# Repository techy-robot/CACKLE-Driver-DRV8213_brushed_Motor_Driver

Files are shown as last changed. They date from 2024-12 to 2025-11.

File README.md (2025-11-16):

---
modified: 2025-11-07T22:06:51-07:00
---

# DRV8213 brushed Motor Driver

> [!TIP]
> This board is part of a larger modular control board ecosystem, [CACKLE](https://github.com/techy-robot/CACKLE)

This is a single motor driver based on the DRV8213RTER Texas Instruments chip. It is capable of 4 amps current in a voltage range of 1.65 to 11 volts. This is basically a 2-pin H-bridge driver with integrated protection logic. Driving one pin with PWM will cause the motor to go in one direction, driving both pins will cause braking, and disabling both pins will enable coasting.

The chip has one current sense output, which is tied to both ADC pins A and B on the driver module. Pin C of the ADC pins is tied to FAULT, which is pulled low on triggering.  Motor control inputs are on Pins A and B, and the motor output is through a JST PH (2mm Pitch) 2-pin connector which matches the same pin order as the input. The JST-PH connector is 5mm high and is positioned near the center of the board.

The module is a 4-layer PCB with additional exposed traces for the power and ground to add solder for more current carrying capability. I designed it to carry 10 amps with 1 oz outer copper and 0.5oz inner copper, which can be increased to 20 amps current by adding solder. This was the cheapest method to go with, since 2 oz copper would add an additional 30$ per 5 boards. 

Schematic PDF

3D model:
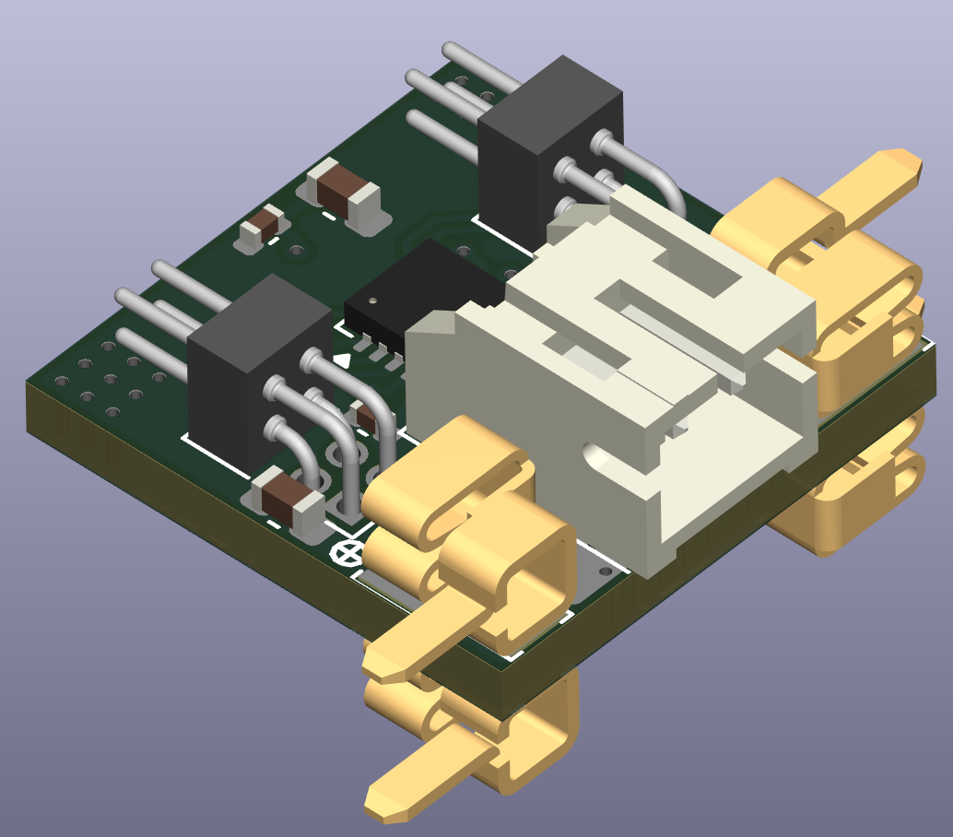
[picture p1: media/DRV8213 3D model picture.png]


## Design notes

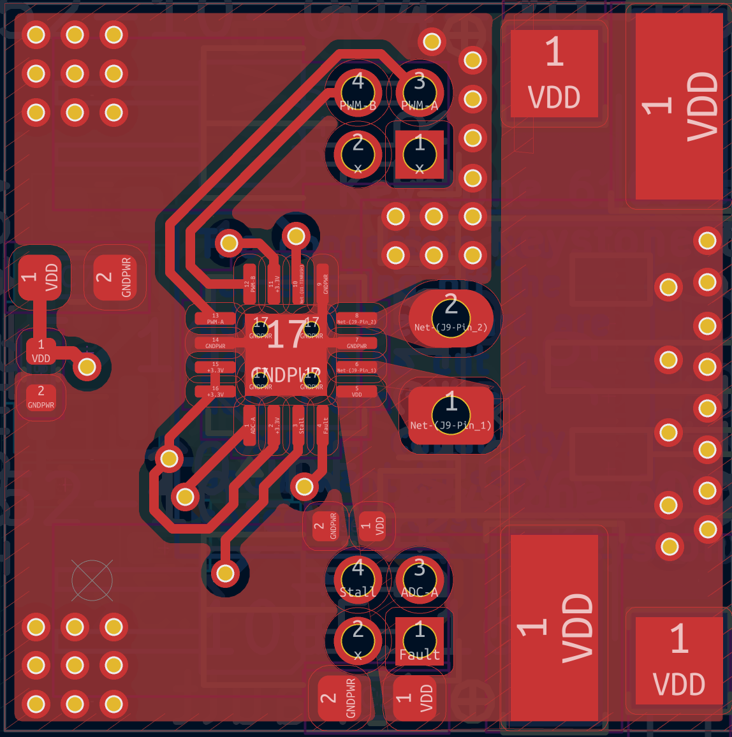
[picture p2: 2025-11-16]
media/DRV8213 Top.png

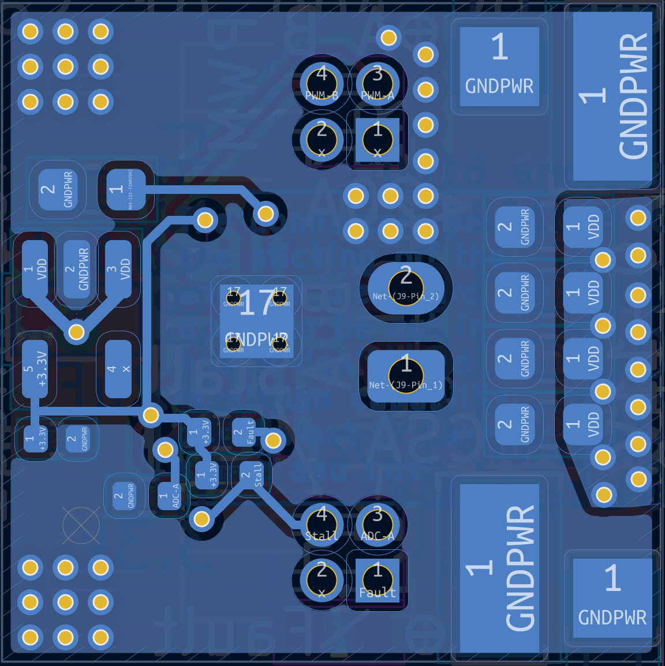
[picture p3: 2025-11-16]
media/DRV8213 Bottom.png

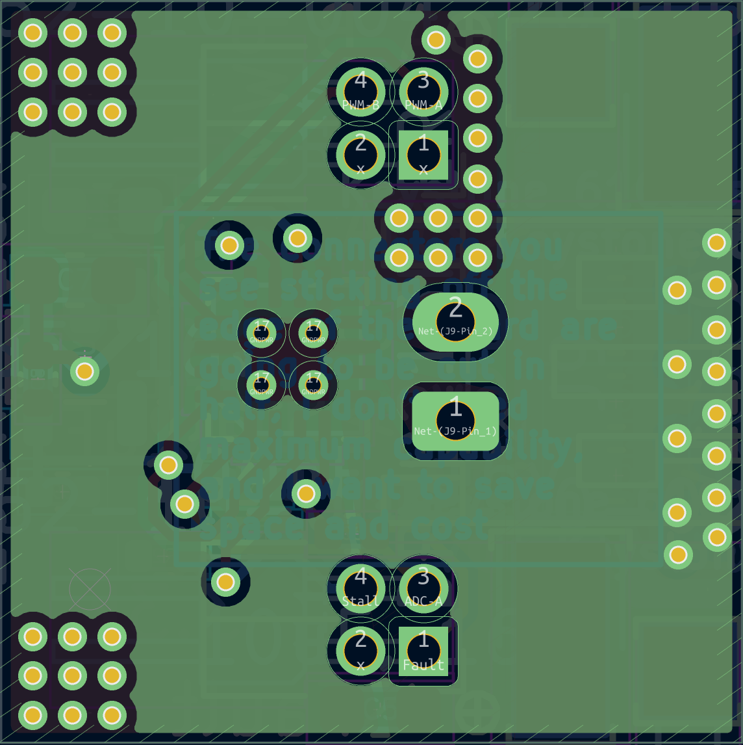
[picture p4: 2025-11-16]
media/DRV8213 In1.png

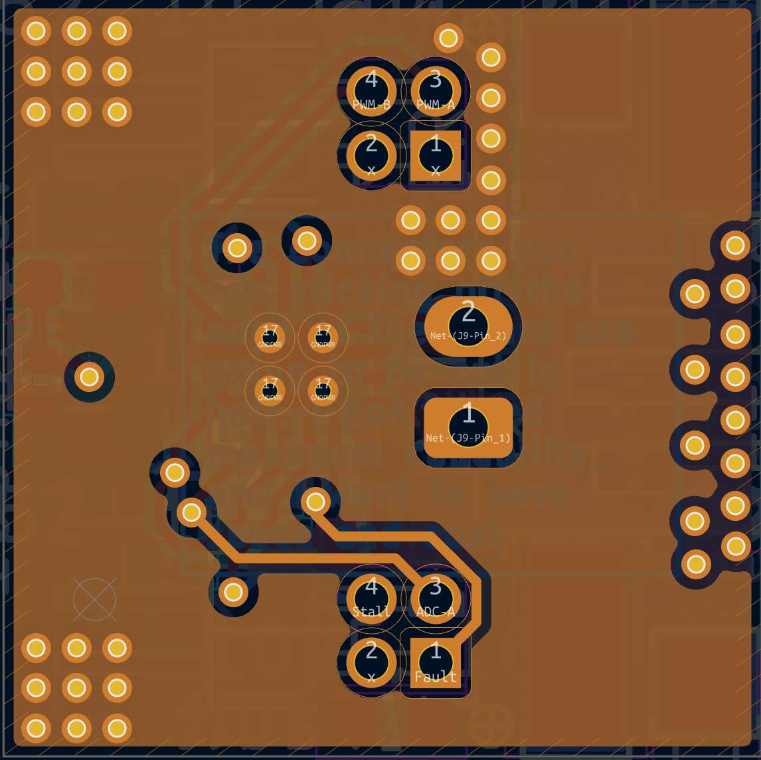
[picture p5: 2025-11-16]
media/DRV8213 In2.png

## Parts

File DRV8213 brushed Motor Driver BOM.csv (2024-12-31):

Id | Designator | Footprint | Quantity | Designation | Supplier and ref
1 | J3,J2,J7,J6 | Keystone_3579 | 4 | Keystone 3579
2 | J4,J1,J8,J5 | Keystone_3569_half | 4 | Keystone 3569
3 | C6,C8 | C_0402_1005Metric | 2 | 100nF, 16v
4 | J11,J10 | PinHeader_1x03_P1.27mm_Horizontal | 2 | 1.27mm pin header
5 | C7,C1,C4,C5,C3,C2 | C_0603_1608Metric | 6 | 10uF, 16v
6 | J9 | JST_PH_S2B-PH-K_1x02_P2.00mm_Horizontal | 1 | JST PH 2mm horizontal
7 | U1 | WQFN-16-1EP_3x3mm_P0.5mm_EP1.68x1.68mm_ThermalVias | 1 | DRV8213RTER
8 | C9 | C_0402_1005Metric | 1 | 2.2uF, 10v
9 | R2 | R_0402_1005Metric | 1 | 3.3k
10 | U2 | SOT-23-5 | 1 | LP2981-3.3
11 | R1 | R_0402_1005Metric | 1 | 10k

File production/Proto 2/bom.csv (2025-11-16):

Designator | Footprint | Quantity | Value | LCSC Part #
C1, C2, C3, C4, C5, C7 | 0603 | 6 | 10uF, 16v | C96446
C10 | 0603 | 1 | 33nF | C21117
C6, C8 | 0402 | 2 | 100nF, 16v | C1525
C9 | 0402 | 1 | 2.2uF, 10v | C12530
J1, J2, J5, J6 | Keystone_6102 | 4 | Keystone 6102
J10, J11 | Precidip 852-10-004-20-001101 | 2 | Precidip 852-10-004-20-001101
J3, J4, J7, J8 | Keystone_6100 | 4 | Keystone 6100
J9 | JST_PH_S2B-PH-K_1x02_P2.00mm_Horizontal | 1 | JST PH 2mm horizontal | C160237
R1, R3 | 0402 | 2 | 10k | C25744
R2 | 0402 | 1 | 3.3k | C25890
U1 | WQFN-16-1EP_3x3mm_P0.5mm_EP1.68x1.68mm_ThermalVias | 1 | DRV8213RTER
U2 | SOT-23-5 | 1 | LP2981-3.3 | C129997

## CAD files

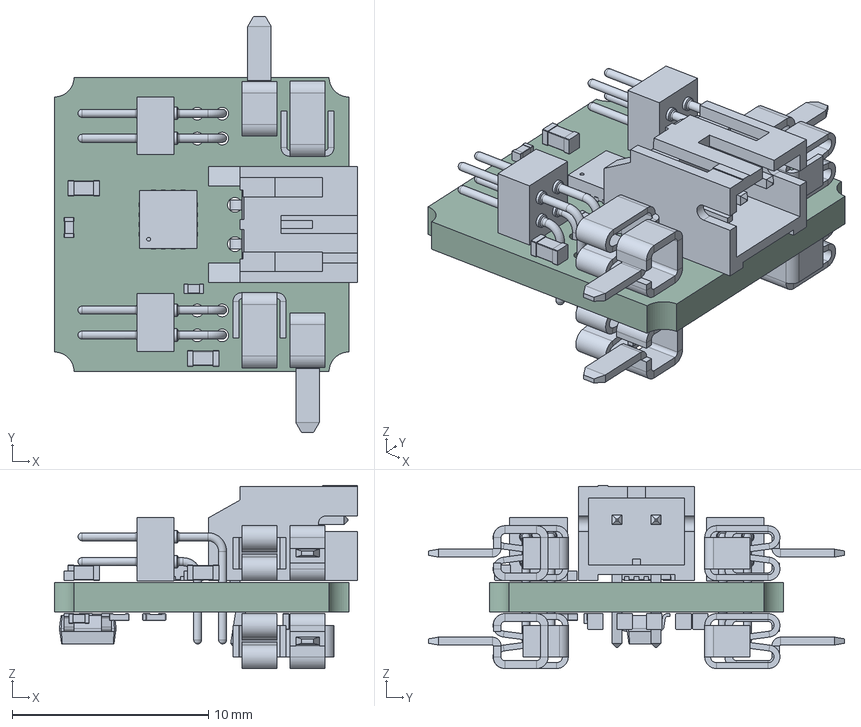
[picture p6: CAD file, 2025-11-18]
DRV8213 brushed Motor Driver.step
15.4 x 21.2 x 9.33 mm
C_0603_1608Metric x 7
C_0402_1005Metric x 3
JST_PH_S2B-PH-K_1x02_P2.00mm_Horizontal
Precidip 852-10-004-20-001101 x 2
WQFN-16-1EP_3x3mm_P0.5mm_EP1.6x1.6mm
R_0402_1005Metric x 3
SOT-23-5
DRV8213 brushed Motor Driver_PCB

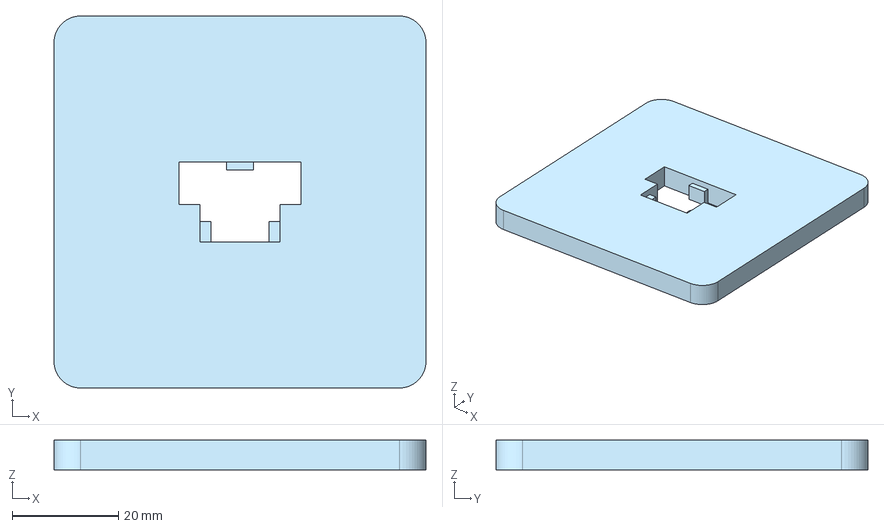
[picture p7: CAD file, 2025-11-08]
DRV8213 2nd side Stencil Jig.step
70.0 x 70.0 x 5.60 mm

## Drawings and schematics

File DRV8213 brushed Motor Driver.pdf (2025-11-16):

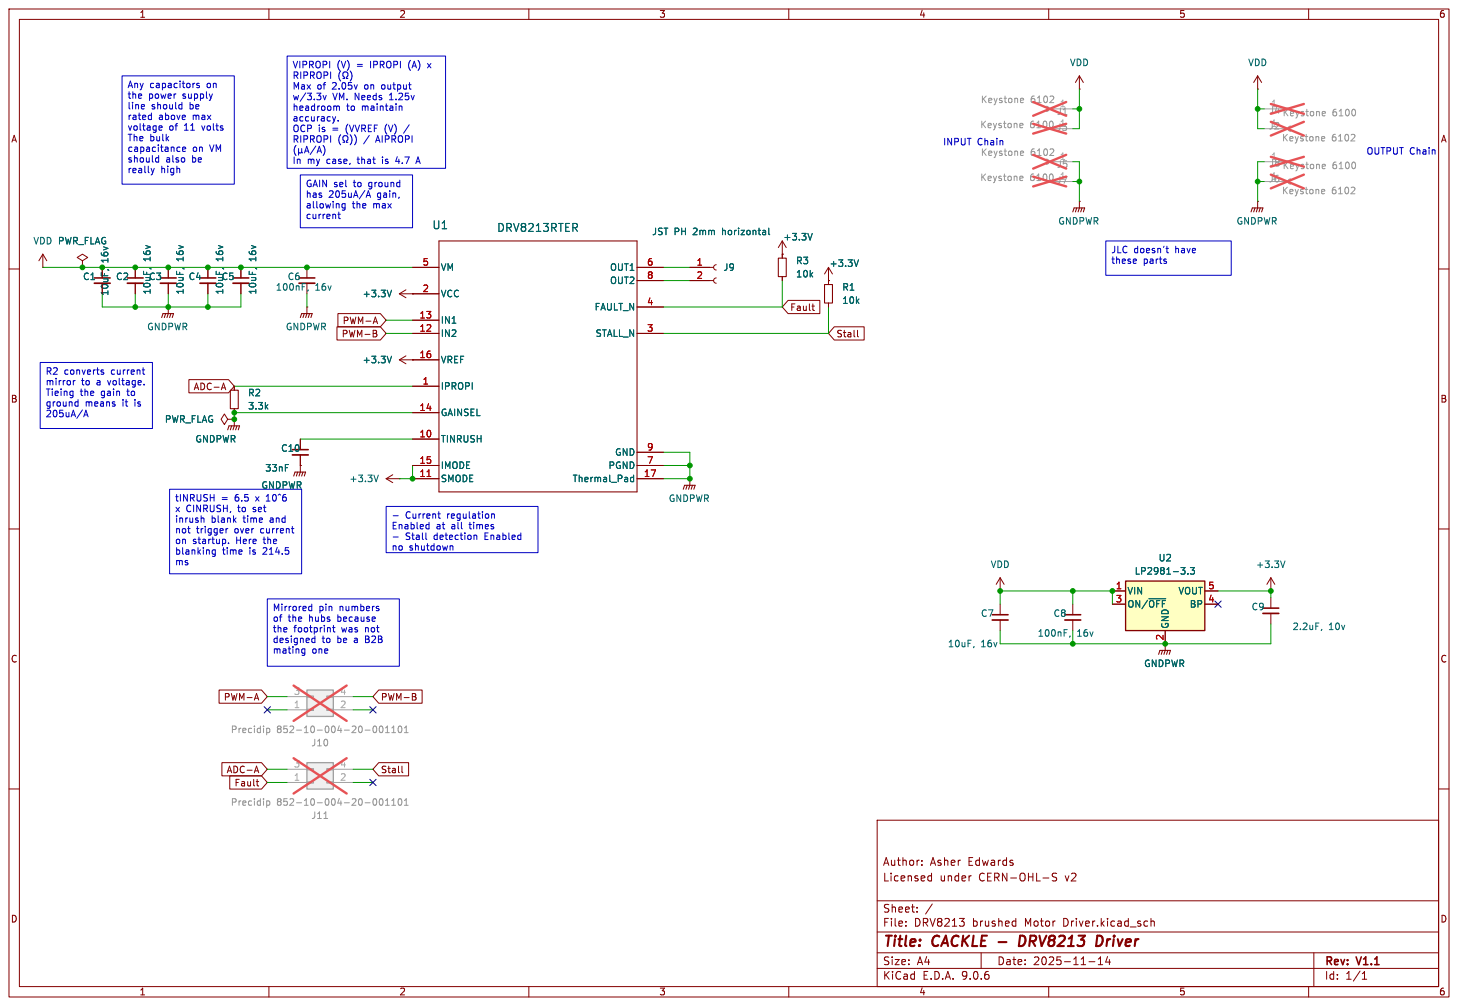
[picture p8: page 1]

the power supply
line should be
rated above max
voltage of 11 volts The bulk

accuracy. OCP is = (VVREF (V) / RIPROPI þÿ(©)) / AIPROPI þÿ(¼A/A)

In my case, that is 4.7 A GAIN sel to ground
1J6 Keystone 6102 C10

current R2 converts current mirror to a voltage.

Tieing the gain to

tINRUSH = 6.5 x 10^6
x CINRUSH, to set
inrush blank time and

- Current regulation Enabled at all times

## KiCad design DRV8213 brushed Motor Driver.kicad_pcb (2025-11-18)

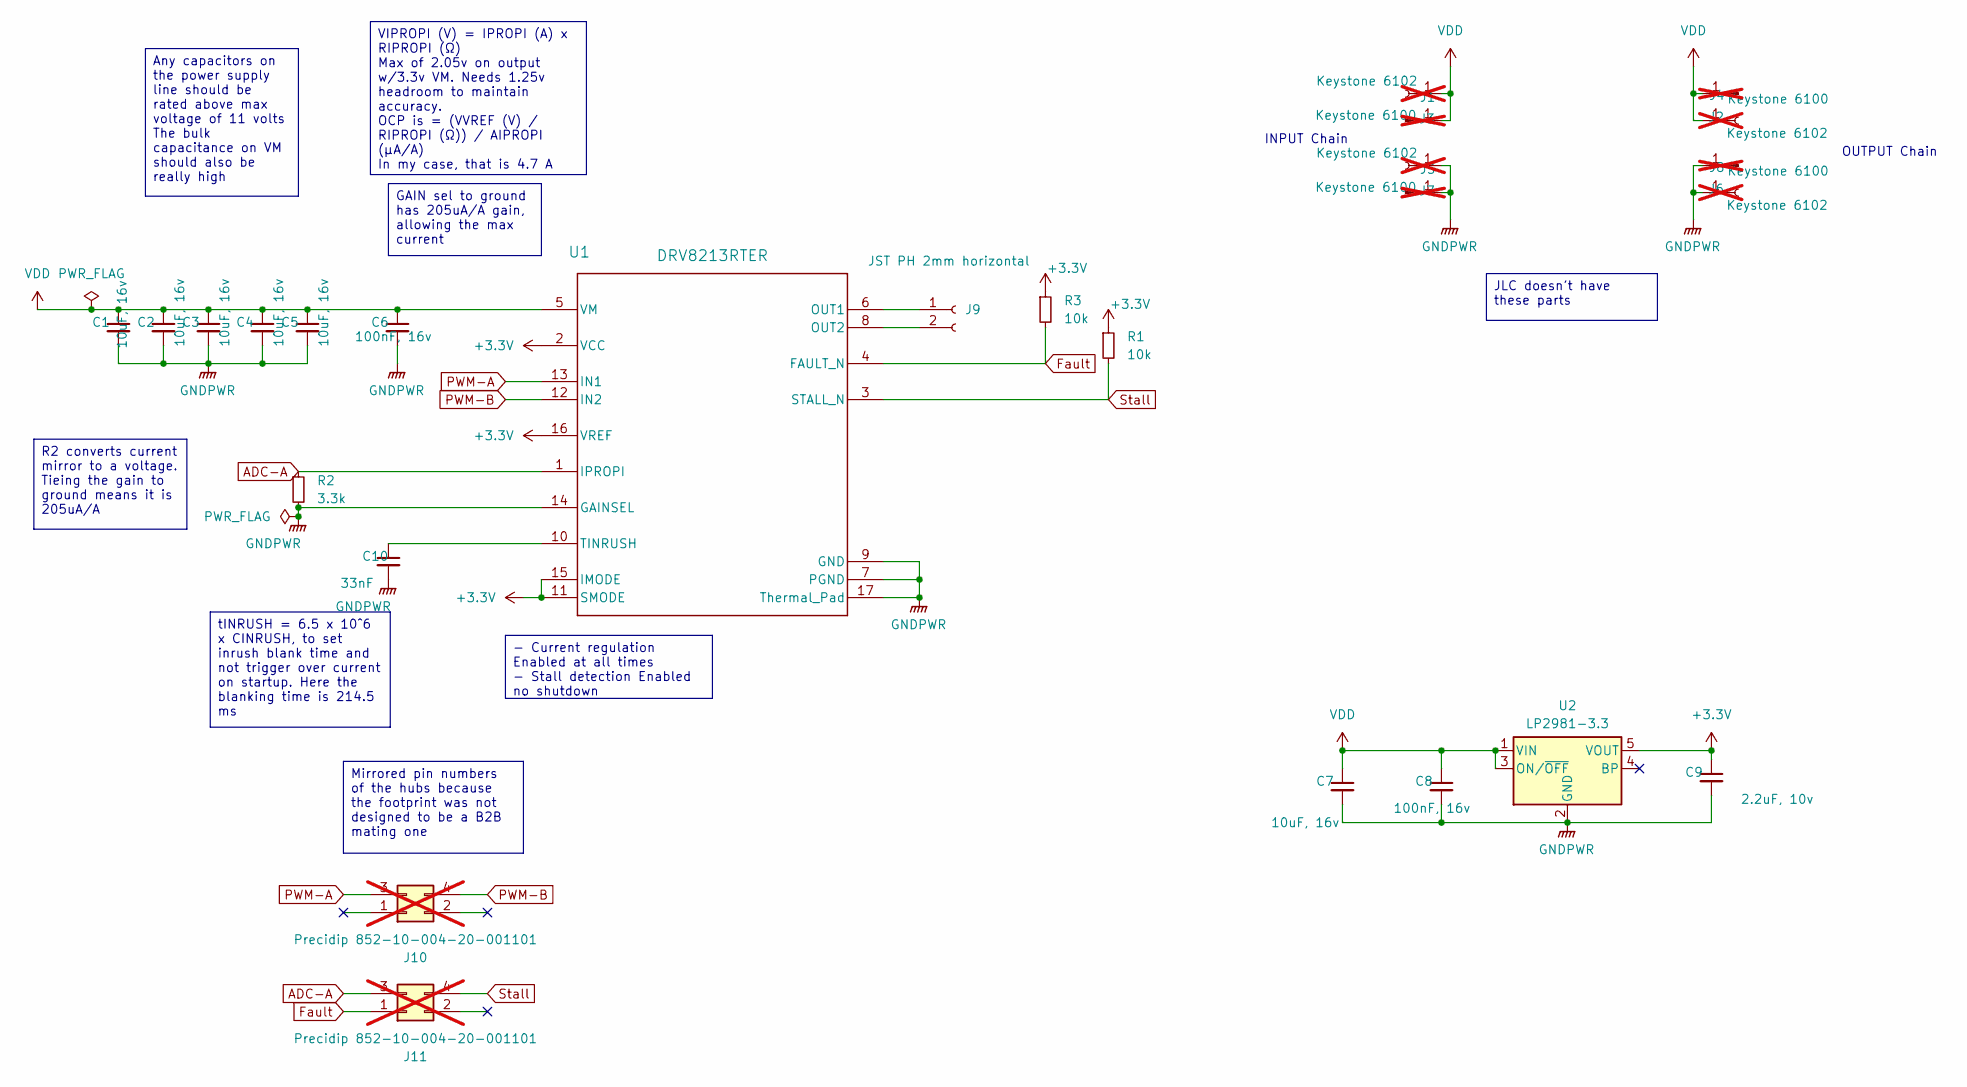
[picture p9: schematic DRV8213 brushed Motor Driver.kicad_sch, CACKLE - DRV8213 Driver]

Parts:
C1, C2, C3, C4, C5, C7: 10uF, 16v; C_0603_1608Metric; LCSC C96446
C6, C8: 100nF, 16v; C_0402_1005Metric; LCSC C1525
C9: 2.2uF, 10v; C_0402_1005Metric; LCSC C12530
C10: 33nF; C_0603_1608Metric; LCSC C21117
J1, J2, J5, J6: Keystone 6102; Keystone_6102; not fitted
J3, J4, J7, J8: Keystone 6100; Keystone_6100; not fitted
J9: JST PH 2mm horizontal; JST_PH_S2B-PH-K_1x02_P2.00mm_Horizontal; LCSC C160237
J10, J11: Precidip 852-10-004-20-001101; not fitted
R1, R3: 10k; R_0402_1005Metric; LCSC C25744
R2: 3.3k; R_0402_1005Metric; LCSC C25890
U1: DRV8213RTER; WQFN-16-1EP_3x3mm_P0.5mm_EP1.68x1.68mm_ThermalVias
U2: LP2981-3.3; SOT-23-5; LCSC C129997

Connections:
+3.3V: C9.1, R1.1, R3.1, U1.2 (VCC), U1.11 (SMODE), U1.15 (IMODE), U1.16 (VREF), U2.5 (VOUT)
ADC-A: J11.3, R2.1, U1.1 (IPROPI)
Fault: J11.1, R3.2, U1.4 (FAULT_N)
GNDPWR: C1.2, C2.2, C3.2, C4.2, C5.2, C6.2, C7.2, C8.2, C9.2, C10.2, J5.1, J6.1, J7.1, J8.1, R2.2, U1.7 (PGND), U1.9 (GND), U1.14 (GAINSEL), U1.17 (Thermal_Pad), U2.2 (GND)
unnamed: J9.1, U1.6 (OUT1)
unnamed: J9.2, U1.8 (OUT2)
unnamed: C10.1, U1.10 (TINRUSH)
PWM-A: J10.3, U1.13 (IN1)
PWM-B: J10.4, U1.12 (IN2)
Stall: J11.4, R1.2, U1.3 (STALL_N)
VDD: C1.1, C2.1, C3.1, C4.1, C5.1, C6.1, C7.1, C8.1, J1.1, J2.1, J3.1, J4.1, U1.5 (VM), U2.1 (VIN), U2.3 (ON/~OFF)

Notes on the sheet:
INPUT Chain
OUTPUT Chain
GAIN sel to ground has 205uA/A gain, allowing the max current
R2 converts current mirror to a voltage. Tieing the gain to ground means it is 205uA/A
VIPROPI (V) = IPROPI (A) x RIPROPI (Ω) Max of 2.05v on output w/3.3v VM. Needs 1.25v headroom to maintain accuracy. OCP is = (VVREF (V) / RIPROPI (Ω)) / AIPROPI (μA/A) In my case, that is 4.7 A
Mirrored pin numbers of the hubs because the footprint was not designed to be a B2B mating one
- Current regulation Enabled at all times - Stall detection Enabled no shutdown
JLC doesn't have these parts
Any capacitors on the power supply line should be rated above max voltage of 11 volts The bulk capacitance on VM should also be really high
tINRUSH = 6.5 x 10^6 x CINRUSH, to set inrush blank time and not trigger over current on startup. Here the blanking time is 214.5 ms

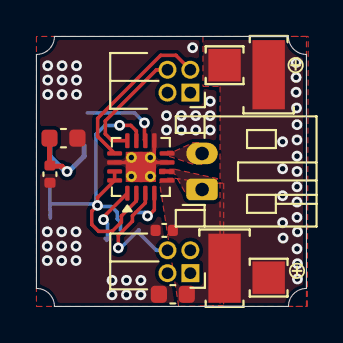
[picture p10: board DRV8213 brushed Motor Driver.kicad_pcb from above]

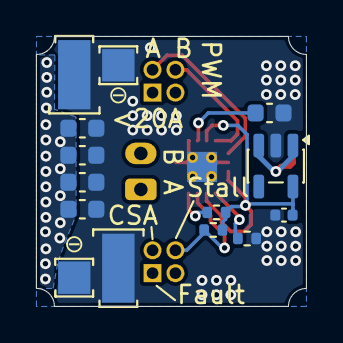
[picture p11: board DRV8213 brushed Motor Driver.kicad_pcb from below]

Board: 4 copper layers, 15.0 x 15.0 mm, 26 parts (14 on the bottom side), 11 nets.

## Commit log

2024-12-31 Rearranged design files
    Instead of "Kicad" the main design folder is now named "Hardware" since I have gerbers and notes besides the kicad files. I have also put my designs in their proper categories.
    [DRV8213 brushed Motor Driver BOM.csv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]
2025-01-01 Updated files for JLC DFM checks
    [DRV8213 brushed Motor Driver.kicad_pcb, DRV8213 brushed Motor Driver.kicad_sch, bom.csv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]
2025-01-02 Added schematic PDFs for all boards
2025-01-04 Added gerber zip files
2025-01-13 Changed link names for schematic embeds not displayin
    In Obsidian I can see the pdf embeds perfectly fine, but Github doesn't want to show embedded PDFs. I changed the link alias to "Schematic PDF" so people know what the link is when it doesn't display
2025-10-10 Moved all current production files to Proto 1.
    I haven't made a 2nd prototype yet
    [DRV8213 brushed Motor Driver-B_Cu.gbl, DRV8213 brushed Motor Driver-B_Mask.gbs, DRV8213 brushed Motor Driver-B_Paste.gbp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]
2025-11-08 Moved stencil jig from monorepo to here
    [DRV8213 2nd side Stencil Jig.step]
2025-11-15 Updated connector parts in schematic
    [DRV8213 brushed Motor Driver.kicad_sch]
2025-11-15 Switched out and arranged new connectors
    [DRV8213 brushed Motor Driver.kicad_pcb]
2025-11-15 Updated date and version
    [DRV8213 brushed Motor Driver.kicad_pcb]
2025-11-15 Split Stall and Fault detection
    [DRV8213 brushed Motor Driver.kicad_sch]
2025-11-15 Clarified 3v3 regulator and caps
    [DRV8213 brushed Motor Driver.kicad_sch]
2025-11-15 Added inrush current blank capacitor
    [DRV8213 brushed Motor Driver.kicad_sch]
2025-11-15 Update ADC pin assignment
    [DRV8213 brushed Motor Driver.kicad_sch]
2025-11-15 Relayout with new components
    [DRV8213 brushed Motor Driver.kicad_pcb]
2025-11-15 Finished reroute
    [DRV8213 brushed Motor Driver.kicad_pcb]
2025-11-15 Hide reference values on silkscreen
    [DRV8213 brushed Motor Driver.kicad_pcb]
2025-11-15 Reversed connector pin assignments to mirror hub
    Technically any pin would work, but I want it logical order with A matching with A. Some hubs may not have enough pins also, so most important pins go first. I might change the footprint numbers to match as well, but this is less important.
    [DRV8213 brushed Motor Driver.kicad_pcb, DRV8213 brushed Motor Driver.kicad_sch]
2025-11-15 Fixed Silkscreen
    [DRV8213 brushed Motor Driver.kicad_pcb]
2025-11-15 Tweaked silkscreen and via placement
    [DRV8213 brushed Motor Driver.kicad_pcb]
2025-11-15 Clarified expected voltage range based on datasheet, updated mask
    [DRV8213 brushed Motor Driver.kicad_pcb, DRV8213 brushed Motor Driver.kicad_sch]
2025-11-15 Removed 3v3 test pad
    [DRV8213 brushed Motor Driver.kicad_pcb, DRV8213 brushed Motor Driver.kicad_sch]
2025-11-16 Fixed connector placement
    It was overlapping a whole millimeter!
    [DRV8213 brushed Motor Driver.kicad_pcb]
2025-11-16 Fabrication outputs
    [DRV8213 brushed Motor Driver.step, bom.csv, designators.csv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]
2025-11-17 Add 1mm round corner cutouts to every edge
    This is a future proofing step for an idea I had, it may not come to anything, but whatever
    [DRV8213 brushed Motor Driver.kicad_pcb, DRV8213 brushed Motor Driver.step, bom.csv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]
2025-11-18 Fixed connector alignment
    [DRV8213 brushed Motor Driver.kicad_pcb, DRV8213 brushed Motor Driver.step, bom.csv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]
2025-11-18 Fixed critical error
    [DRV8213 brushed Motor Driver.kicad_pcb, DRV8213 brushed Motor Driver.step, positions.csv]

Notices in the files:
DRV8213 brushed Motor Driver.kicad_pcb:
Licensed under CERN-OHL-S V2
